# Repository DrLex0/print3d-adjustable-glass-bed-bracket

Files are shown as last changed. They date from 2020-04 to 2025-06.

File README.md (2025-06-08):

# Customizable Adjustable Glass Bed Bracket
*Customizable adjustable bracket for mounting glass plates on the print bed of 3D printers like the FlashForge Creator Pro (formerly thing:1949142)*

### License
[Creative Commons - Attribution - Share Alike](https://creativecommons.org/licenses/by-sa/4.0/)

### Attribution
This is a remix of multiple source models: the original ‘Flashforge Creator Pro Adjustable Glass Bed Bracket’ by chewbone ([Thingiverse thing:1291106](https://www.thingiverse.com/thing:1291106)), which was modified by omegatron ([Thingiverse thing:1296854](https://www.thingiverse.com/thing:1296854)), then by Lochemage ([Thingiverse thing:1940192](https://www.thingiverse.com/thing:1940192)), and then by me.

### Gallery

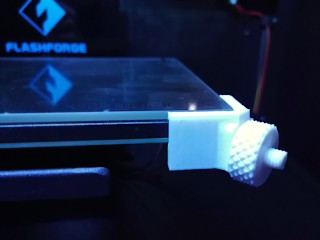
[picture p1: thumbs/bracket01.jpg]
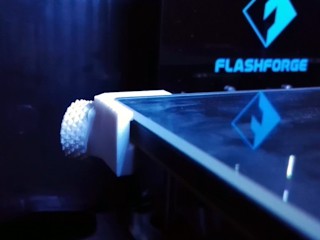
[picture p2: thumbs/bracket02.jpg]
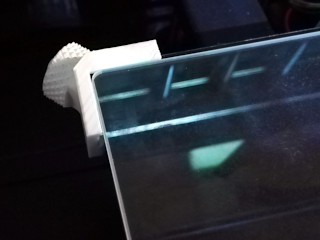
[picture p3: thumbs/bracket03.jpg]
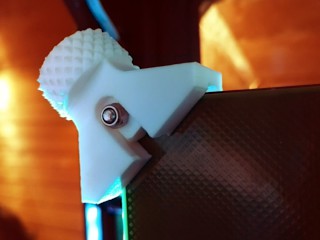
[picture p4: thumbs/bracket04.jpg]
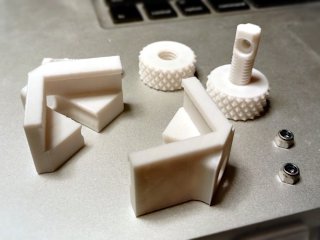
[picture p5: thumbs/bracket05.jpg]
Parts
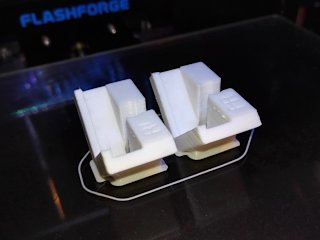
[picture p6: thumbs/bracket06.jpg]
Printing
[🔎](images/bracket01.jpg) [🔎](images/bracket02.jpg) [🔎](images/bracket03.jpg) [🔎](images/bracket04.jpg) [🔎](images/bracket05.jpg) [🔎](images/bracket06.jpg)

*Yes, there's quite a bit of text here, but it's worth it to read all of it. Even if you're familiar with Customizer and printing strong heat-resistant parts, you should still read the ‘Mounting’ and ‘Using’ sections for some important hints.*

## Intro

This is yet another iteration of the adjustable glass bed bracket. This time, not only the bracket itself is adjustable, so is the model! This customizable bracket fits the FlashForge Creator Pro and printers with similar build plates with M3 bolts at their corners. The adjustable knob makes it easy to swap out glass plates if you have more than one, so you can start printing on another plate while the first one is still cooling down.

The main advantage of this design is that it allows to mount the glass plate without anything sticking out above it. This means you never need to worry about the risk of your nozzles crashing into the brackets. This particular remix improves upon the originals by not sandwiching the bracket between the bed and the pin. This makes it much easier to adjust the bracket, and it also offers a more balanced mount.

If you have yet to buy a glass plate, try to find one that is just a few millimeters smaller than the bed in both the X and Y directions, and has rounded or beveled edges. Such plates work best with these brackets. **Borosilicate glass** is highly preferred over regular glass. Avoid plates thicker than 4 mm: they will take long to heat, and because glass is a rather good thermal insulator, their surface temperature will be a lot lower than expected.

*Obvious disclaimer:* I am not responsible for any possible damage caused by the use of these brackets, not if you follow my advice, and certainly not if you ignore it.
 

## Creating a customized bracket

Do not just print the example STL file, it is unlikely to fit your setup. Instead, open the `.scad` file in [OpenSCAD](https://www.openscad.org/) and **[use the OpenSCAD Customizer](https://www.dr-lex.be/3d-printing/customizer.html)** to generate brackets that match your particular bed and glass dimensions. The Customizer is limited to plates roughly the same width and depth as the heated bed itself.

If you are making brackets for a popular combination of printer model and glass bed, consider saving your parameters as a new customizer preset. The preset will be saved in the `.json` file and it would be nice if this would then be included in this repository, such that other users having the same printer and bed could simply load that preset from the customizer UI. To allow this, send me your updated `.json` file (for instance through a pull request).

Measure the *width, depth and height* (in other words *X, Y* and *Z* dimensions) of both the glass plate(s) and the bed (without glass). Next, enter those values in the corresponding fields in Customizer. Be as accurate as possible! Aim for at least 0.5 mm accuracy, this is possible with a simple ruler and a keen eye.
If you have multiple supposedly “identical” plates, there will often be small differences between them: take the *minimum* width and depth across all plates.

You can opt to mount the brackets on the front right and rear left corners, or front left and rear right. One pair of brackets is sufficient, but should you want to clamp all corners anyway, just run Customizer twice for both configurations. The models are marked so you know where to mount them: *FR = front right, FL = front left, RL = rear left, RR = rear right.*

The default is to center the glass on the print bed, but if you want to align one of its edges to an edge of the bed, you can select that in the options. For instance, I have aligned mine to the front edge because my start G-code chops off oozed filament on that edge.

You can choose to add an extra pair of tiny *ridges* that may help to keep the plate clamped down, an explanation can be found below.

The option *‘Rear Corner Fix’* in the advanced settings compensates for an oddness of the FFCP (at least mine). This is also explained below. Don't forget to disable this if you are generating brackets for printers with a different bed design.

If your glass plate is larger than the bed, you may want to enable *‘allowTabInset’* in the advanced settings to allow the glass to extend somewhat into the edges of the bracket. This option is disabled by default because it could make the bracket weaker. If the glass extends much more in one direction than the other, the inset will only occur for one edge to ensure alignment. Avoid that situation, and again: avoid plates larger than the bed altogether.

If the generated 3D model shows **“FAIL,”** then either you've entered non-numerical dimensions, or your glass plate is unfortunately too large or small to be compatible with the brackets. You can try to fiddle with the advanced settings if the dimensions are borderline, but it is advisable to find some other glass instead, that has nearly the same size as the bed.

### When to use the ‘Extra ridges’ option

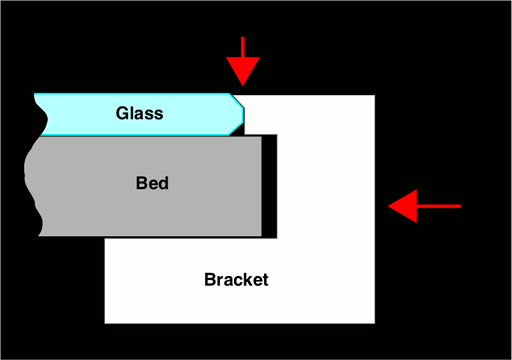
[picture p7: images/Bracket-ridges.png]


If your glass has beveled or rounded edges, it is worth it to enable the *‘Extra ridges’* option in Customizer. As the figure shows, the ridges can clamp down the glass by grabbing it on the bevel. This is not strictly necessary when using borosilicate glass, but regular glass or other materials that have a significant coefficient of expansion, are more likely to warp and lift at the edges when the bed is heated.

If you want to have the same clamp-from-above effect with glass that has straight edges, you can only do so by ignoring my advice of never letting anything stick out above the glass. If you make the brackets about 0.2 mm taller than the glass and enable the ridges, they will also clamp the glass from above. This is not worth the risk however: trying to clamp down the glass is *pointless* if you follow my usage instructions.

### When to enable/disable the ‘Rear Corner Fix’ option

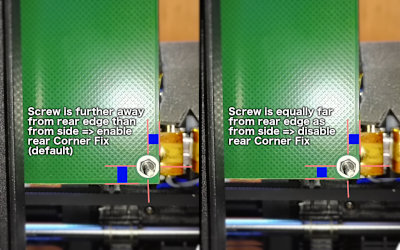
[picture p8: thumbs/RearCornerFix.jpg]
[🔎](images/RearCornerFix.jpg)

The bed on my FFCP isn't perfectly symmetrical and by default, the models will be generated to compensate for this. Check the bottom side of your heated bed at the rear (hint: use a mirror or take a snapshot with your smartphone) and compare it to the photo. If it looks like in the left photo, you don't need to change anything to the defaults. If it looks like in the right photo, disable the ‘Rear Corner Fix’ in the advanced settings.
 

## Choosing What Parts to Print

Next to the customized bracket model you created above, you will also need to print one pin and one nut (knob) per bracket. These are the choices you need to make:

* **Print spring-loaded knobs or not?** If you're willing to spend a little extra time molding silicone gaskets or printing them with a flexible filament, it is well worth it to print the spring-loaded knobs from the *SpringLoadedKnobs* folder instead of the plain ones. The springs ensure that the glass remains clamped regardless of differing thermal expansion of the heated bed versus the glass plate.
* **Print pins and nuts with fine or coarse thread?** The coarse thread is easier to print but offers rougher adjustment. I recommend to try the fine thread first.
* **Print regular or small knobs?** You only need the smaller ones if you have a thin bed and the regular size knob would stick out above the glass. Otherwise the regular ones are easier to adjust.
* **Print regular or extra long pins?** The *XL* versions of the pins are slightly longer than the normal ones. Only print the longer ones if necessary, because printing them in ABS or PC will be even more difficult than the shorter ones. If these still are too short, you definitely need to find a glass plate that more closely matches the size of the heated bed.
* **Print hollow or solid pins?** In most cases you should print the hollow one, it is less likely to warp during printing. Only use the solid one if you have a good reason. (There is no hollow version of the coarseThread because its shape leaves no room for a hollow space.)
 

## Printing

*This must be printed in a material that can withstand the heat of the heated bed!*

The model that comes out of Customizer is ready to print _without supports_. The worst overhangs are 45°, which should be easy to print if you have tuned your printer well. A fan can help with the overhangs but if you print ABS, either reduce fan speed if you can, or print hot and slowly.

If the pins seem too thick to fit inside the knobs, you can try re-printing the knobs scaled to 102% or more in the XY plane. (Mind that this is a sign that your printer is not printing accurately and you would be better off fixing the root cause of that problem than doing workarounds like this.)

I printed the nuts and pins at 0.1 mm, the bracket at 0.2 mm. I printed extra slowly for additional strength. I used a brim on the corner pieces, but this was probably unnecessary. Print the pins at 100% infill. Infill for the other parts doesn't really matter, but I do recommend to print them with 3 perimeters for strength. To get the best detail on the threads of the pin, print slowly with the fan enabled if necessary. If you really have trouble printing the pins, you might try printing them upright, or use the ‘coarseThread’ versions instead.

The **material** choice is important. Most crucial are the pins, because they are pushed against the heated bed, hence must be the most heat-resistant. What material you need, depends on the maximum temperature to which you will heat the bed during everyday use.
From best to worst, here are some choices for the most common filaments:
* **Polycarbonate (PC):** this is an excellent material because it can withstand all reasonable heated bed temperatures, therefore if you print the brackets with it, you will never have to worry about the bed temperature. I would recommend it if you will often print ABS at bed temperatures near 110°C. Unfortunately PC is difficult to print with. The absolute minimum extruder temperature is [260°C](http://reprap.org/wiki/Polycarbonate#Heater_Settings). You need an all-metal hot-end to print at that temperature, because the teflon liners in standard hot-ends will quickly degrade at that temperature, releasing toxic fumes. You can of course order a PC print through a service like 3DHubs. If price is an issue, it is OK to have only the pins printed in PC, and print the brackets and knobs yourself in ABS.
* **ABS:** this is a good material because it will not easily deform below 110°C. If you will mostly print PLA and PETG, and only occasionally ABS, then ABS brackets are perfectly OK. You might need to print new pins from time to time because they may bend after a while. To minimize deformation, always follow the instructions from the *Mounting* and *Using* sections!
* **PETG:** this is good if you will never heat the bed above 75°C, e.g. if you'll only print PLA and occasionally PETG. Don't use it if you will ever have to do an ABS print though.
* **PLA:** I would not recommend this, unless you'll never heat the bed above 55°C. If you would ever need to heat the bed above 60°C, your PLA pins and brackets will deform or melt.

I have used ABS printed pins for about half a year, after this they were somewhat bent but still usable. I printed new pins in polycarbonate, and I expect those to last forever.

If you're the [AvE](https://www.youtube.com/user/arduinoversusevil) kind of guy and have the tools and skills for metalworking, an alternative to obtain perfectly heat-resistant pins, is to buy stainless steel M8 × 1.25 bolts and transform them into the shape of the pins, or create the shape from scratch. Stainless steel is ideal due to its low thermal conductivity, which reduces the need for heat-resistance of the other parts of the bracket.
 

## Mounting

This design differs from the originals it was remixed from, in that you do not need to unscrew any of the existing nuts or bolts (except possibly on newer printers, see below). Instead, you need an additional M3 nut per pin. I recommend to use *nyloc* nuts. Mount the pin with the recess upwards, covering the existing M3 nut, and tighten the pin with the extra M3 nut ([this tool](https://www.thingiverse.com/thing:1959962) may come in handy).

See the following rendered 3D image for an illustration of how the complete assembly fits together. Again, even though this image shows the screws separately, you do not need to remove them. This was only rendered as such to help people who are building their printer from scratch.

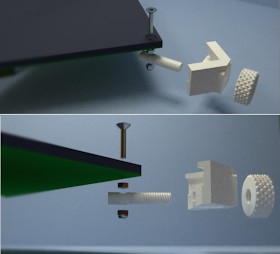
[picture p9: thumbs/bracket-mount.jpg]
[🔎](images/bracket-mount.jpg)

*Important:* only tighten the M3 nut just to the point where the pin can no longer move vertically. Do not tighten it further, unless you printed the pin in polycarbonate or will never heat the bed anywhere near 110°C.

If you don't have any M3 nuts to spare, you can also print the pin from [omegatron's original model](http://www.thingiverse.com/thing:1296854) and mount it using the existing nut, with the recess downwards. I do recommend using my version of the pin if possible.

*Note:* the Creator Pro used to ship with bolts on the corners of the print bed that were about 20 mm long in total, making them stick out about 11 mm below the bed. It seems that recently FlashForge switched to shorter bolts, which makes it impossible to mount the pins as-is. If this is the case for your printer, you will need to replace the bolts with longer ones. Look for 20 mm M3 bolts with a flat head, preferably also with a hex socket.
 

## Using

If you use the *spring-loaded knobs,* read the instructions from their README, and skip the following paragraph because those knobs make it redundant.

Otherwise, the correct workflow is to first **preheat** your bed with the glass plate on top, and only tighten the knobs when the temperature is stable. The reason is that borosilicate glass has a much lower thermal expansion coefficient than the bed, therefore if you would tighten it cold and then heat, the bed will become larger w.r.t. the plate, and it may be loose enough to wiggle around. The whole point of these brackets is that it is very easy to adjust them, so it is better to adjust them when not really necessary, than *not* to adjust them when needed.

Do not tighten the knobs like crazy. Just tighten them up to the point where the glass cannot move. Over-tightening may cause the plastic to deform, or the plate to lift if you did not print the brackets with accurate dimensions.
 

### Should you remove the blue sheet or BuildTak when using a glass plate?

If you don't foresee that you will ever print on the sheet again, you should remove it. The sheet acts as an insulator and will cause a drop in temperature between the bed and glass, as much as 10°C depending on the temperature and thickness of the sheet. One small advantage of leaving the sheet installed, is that it provides some friction, making it less easy for the glass to slide around than on the bare metal surface. However, it should be the brackets that keep your glass in place, not the surface.

## How I Designed This

I took omegatron's model, cleaned it up in Blender, and chopped off all the parts that would vary when making it customizable. I exported it to STL, and converted this to an OpenSCAD polyhedron using stl2scad, because Customizer does not allow importing STL files. Then I added the necessary customizable shapes using the usual SCAD magic.

After 8 years, someone notified me that the fine screw threads of the pin and nuts didn't match… yeah. This flaw has been in the models since chewbone's original. It somehow still worked in most cases, but I finally corrected the threads in the v4 nut STL files for optimum performance.

## Updates

### 2016/12/11
I updated the pin model to be longer at the side of the bed. This should make it more resistant against deformation. If you print new pins, be sure to use this new model. Remember: do not tighten the pins any harder against the bed than necessary. Otherwise you'll end up with the counter-intuitive situation where the pin becomes the more loose, the more you tighten it.
Included *‘divided’* variation of the pin model (this had a cavity that might allow to print the threaded part with less infill, however this was unpractical so I removed it again).

### 2016/12/12
Allowed larger range of values in customizer: bed thickness can now go down to 5 mm and tabs can go up to 7 mm.

### 2016/12/27
Added smaller nuts and coarse-threaded variants (using the same threads as Lochemage's remix of the original brackets).

### 2017/05/09
Completely overhauled Customizer so it is much easier to use, and offers a wider range of parameters.
Created [Spring-loaded Knobs remix](http://www.thingiverse.com/thing:2313598), which I highly recommend over the plain knobs.

### 2017/05/14
Added ‘Rear Corner Fix’.
2017/06/04: Bumped default tabWidthOffset from 1.2 mm to 1.5 mm.

### 2017/06/18
Added a version of the regular pin with the threaded section hollowed-out. This makes it less likely to warp when printed in ABS or polycarbonate.
Fixed the broken preview in Customizer/OpenSCAD.
Minor update 2017/07/25: made error messages in customizer preview more readable.

### 2017/08/19
Added XL versions of the pins, these are about 6mm longer.
Wasted some of my precious time due to the stupid “Token Expired” bug in the Thingiverse site. If this kind of crap keeps happening, I'll just stop uploading models altogether.

### 2019/04/07
Added (advanced) option to change the length of the sides of the bracket.

### 2025/06/08
Fixed the incorrect fine screw thread pitch of the nut models, the new ones are now called ‘v4’.

## TAGS:
`Adjustable`, `customizable`, `customizer`, `FFCP`, `FFCPRo`, `glass`, `Glass_bed`, `Glass_bed_holder`, `openscad`, `supportless`

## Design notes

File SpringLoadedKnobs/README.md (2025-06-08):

# Spring-loaded Knobs for Adjustable Glass Bed Bracket
*Knobs with built-in spring action for adjustable glass bed brackets (formerly thing:2313598)*

### License
[Creative Commons - Attribution - Share Alike](https://creativecommons.org/licenses/by-sa/4.0/)

### Attribution
See attribution info in the top-level README.

### Gallery
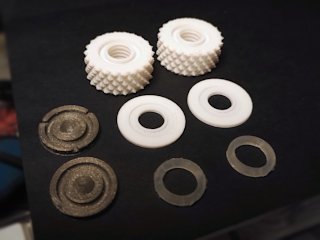
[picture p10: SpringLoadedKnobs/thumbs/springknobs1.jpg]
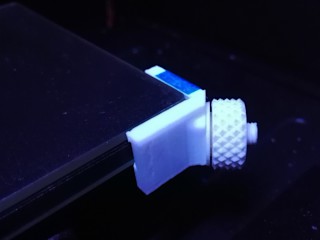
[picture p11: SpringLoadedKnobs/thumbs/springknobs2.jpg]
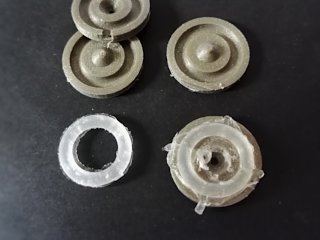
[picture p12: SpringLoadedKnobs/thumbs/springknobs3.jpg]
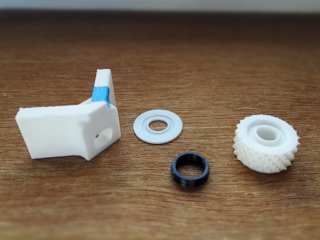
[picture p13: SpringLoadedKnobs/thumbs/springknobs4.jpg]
Photo 4 - TPU spring
[🔎](images/springknobs1.jpg) [🔎](images/springknobs2.jpg) [🔎](images/springknobs3.jpg) [🔎](images/springknobs4.jpg)

## Description and Instructions

These are improved knobs for the Customizable Adjustable Glass Bed Bracket for the FlashForge Creator Pro and similar printers. These knobs have a **silicone gasket** incorporated in them, which acts as a spring. As an alternative, you can print the springs using a **flexible filament.**

The problem with the original knobs and many other bracket designs, is that the thermal expansion of the aluminium bed is much larger than that of the glass (especially borosilicate glass). This means if you tighten the knobs while the bed is cold and then heat it, it becomes larger than the glass. This causes the brackets to lose their grip, allowing the glass to shift around.

These spring-loaded knobs solve that problem by keeping on pushing against the brackets even if they move inwards a little due to the bed expanding. The gaskets are just thick enough to offer the required spring travel, without being too thick to make the brackets wobbly.

Some assembly and patience is required: you need to create your own silicone gaskets with a printable mold, or you can print them with a flexible filament. I provide molds for 3.5 mm and 4 mm tall gaskets. Which one is most suitable, will depend on how flexible the silicone compound is that you will be using. I suggest to simply print both molds, make two pairs of gaskets, and see which ones work best.
 

## Method 1: make gaskets using silicone compound

Carefully read the instructions on the [Customizable Gasket Mold Maker page](https://www.thingiverse.com/thing:2287689). In a very short nutshell: print the molds in **ABS,** as it seems to adhere the least to silicone compound. Use **RTV silicone** if you can.
If you want even thicker gaskets, you can make your own with Customizer on that page. The inner diameter must be *10 mm* and the outer diameter *14.1 mm.* You could also try a gasket with a square profile to increase stiffness.

The nice thing is that you can already use the knobs without the gaskets while you're waiting for them to cure. You only need to remember to manually re-tighten the knobs after preheating the bed. Once you have the gaskets, unscrew the knobs, drop in the gaskets, and you're good to go.

### Preparing the gaskets for use

Cut or pry off any excess silicone from the gaskets to make them nice and round. Make sure the gaskets are fully cured before assembling the knobs. RTV silicone gaskets should be ready to use, but for regular silicone, you should leave the gaskets in the open air for at least 24 more hours, probably longer for neutral cure compound. This allows them to cure further and release solvents still contained inside. Again, exposing them to humidity may speed up this process.
 

## Method 2: print gaskets/springs with flexible filament

If you have a sufficiently flexible filament, you can print an effective spring instead. The `Gasket-TPU-printable` STL file can be printed as-is in TPU. Infill doesn't matter because the model is a hollow shape. The filament must be elastic and reasonably heat-resistant. I have tried this in NinjaFlex which seems to work well. Anything much harder than Shore 85A is likely to be too stiff to act as a spring.
 

## How to use the knobs

Remove any remains of hairspray or glue stick from the bottom of the disks and brackets, to ensure these parts can easily slide against each other, otherwise tightening the knobs could be difficult. A wee bit of silicone grease/oil can help as well, you may need to re-apply this occasionally. Assemble and mount the knobs as shown in the photos.

You can adjust the knobs in two ways:
1. Preheat the bed to the highest temperature you'll use, and then tighten the knobs just beyond the point where the glass can no longer move.
2. Just tighten the knobs with the bed cold, to the point where there is only a tiny gap left between the disk and the knob.

Either method is OK, but the first one is preferred because it minimizes the amount of stress on the brackets and could prolong their lifespan. If you're not going to print for a while, it is advisable to loosen one of the knobs.

If you made the gaskets with regular silicone compound, they will be quite soft when freshly made, and become harder over the course of the next weeks. This means you may need to tighten the knobs more with freshly made gaskets.
 

## Printing

For the **knobs/nuts:** as with the originals, **ABS** is recommended for heat resistance. Print slowly and if possible, provide moderate cooling to get an accurate result. See the main README in the top level of this repository for more details.

All these parts should be printed at 0.1 mm layers. Infill doesn't really matter.

The knobs are available in both fine and coarse threads, and normal and small sizes, like the originals. Print the knob that matches the pin thread and bracket height you're using. You should print the normal size knobs unless you have a very thin bed that would cause the knobs to stick out above the glass.

For the **gasket mold:** again see the [Customizable Gasket Mold Maker page](https://www.thingiverse.com/thing:2287689) for instructions. In a very short nutshell: use **ABS** because it seems the least sticky to the silicone.
To avoid that the tip of the alignment cone becomes a molten blob due to short layer print times, you can try to:
* print two molds at once. You'll need two gaskets anyway, and making them at once will save you a lot of waiting time. It isn't worth it to try saving a few grams of filament by only printing one mold!
* print the molds together with something else to increase the time between layers.
* provide all the cooling you can muster while the cone is being printed.

For the **printable gasket/spring:** just print it in a sufficiently flexible/elastic filament, like NinjaFlex or similar. When in doubt, set infill to 100% although this shouldn't matter because the model is hollow.
 

## Background Information

The reason why I chose silicone gaskets as springs, is that silicone does not easily lose its shape over time, it is quite heat-resistant, and most importantly, everyone can easily make their own gaskets with a 3D printed mold! Any other 3D printed glass bed bracket that relies on springiness of the shape itself, is pretty much doomed to deform over time, especially when heated near 110°C. These knobs on the other hand should last a long time.

## Updates

### 2020/03/07
Added printable spring/gasket that should work well in a soft TPU like NinjaFlex.

### 2025/06/08
Fixed the incorrect fine screw thread pitch of the nut models, the new ones are now called ‘v4’.

## TAGS

`Adjustable`, `FFCP`, `FFCPRo`, `glass`, `Glass_bed`, `Glass_bed_holder`, `knob`, `nut`, `silicone_mold`, `spring_loaded`

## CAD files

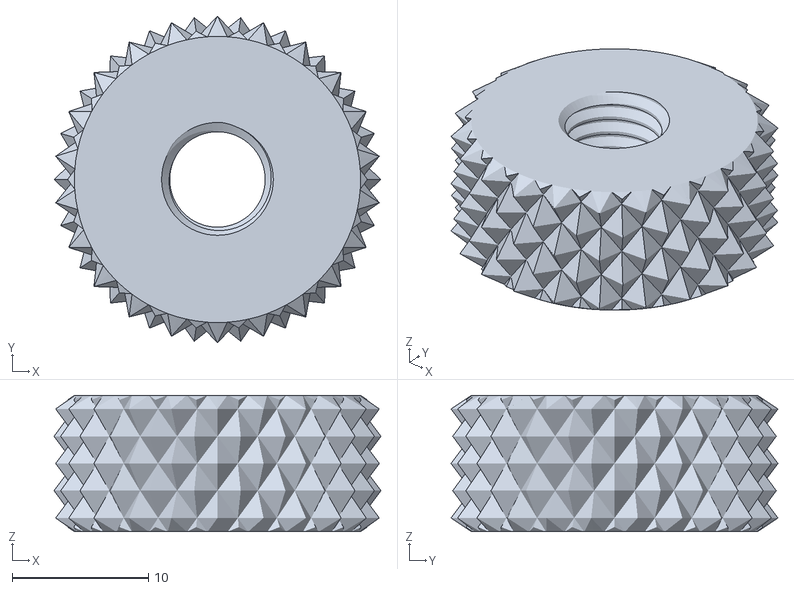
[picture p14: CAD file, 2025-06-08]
GlassBedNut-v4.stl
24.0 x 24.0 x 10.0

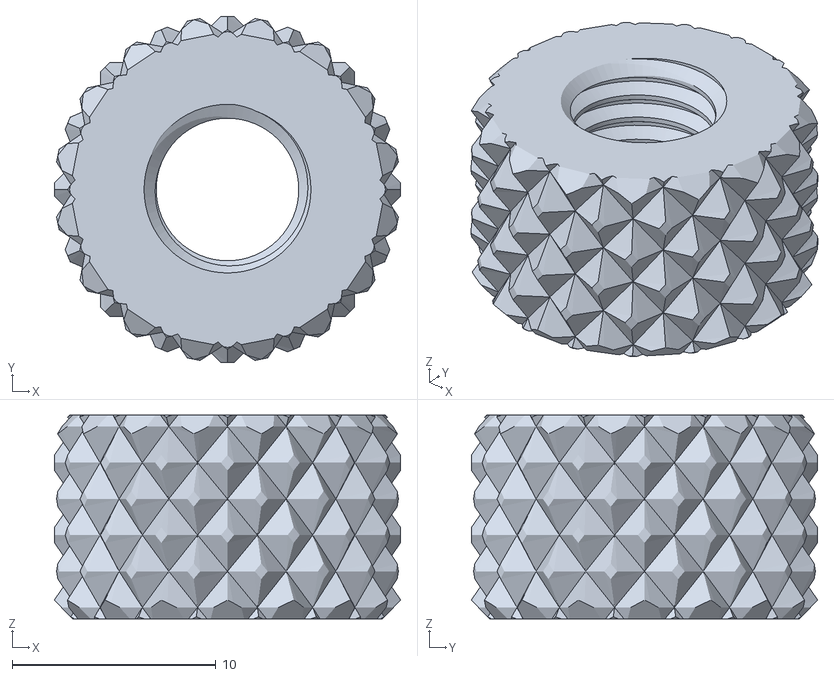
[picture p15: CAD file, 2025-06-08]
GlassBedNut-v4-small.stl
17.0 x 17.0 x 10.0

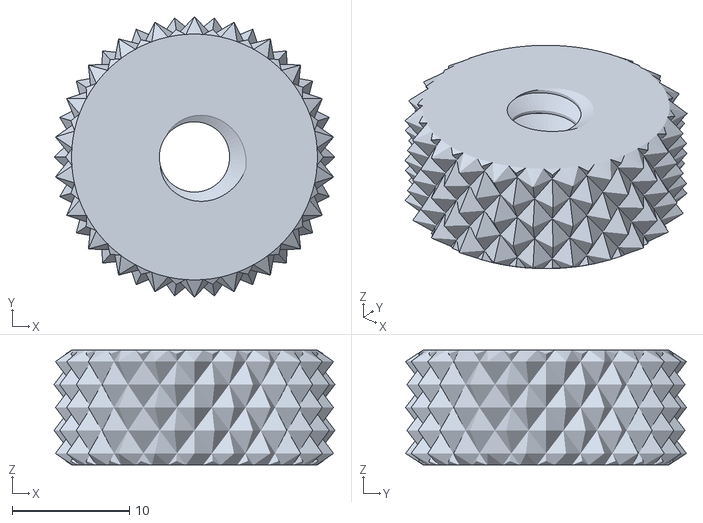
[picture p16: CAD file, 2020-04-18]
GlassBedNut-coarseThread.stl
24.0 x 24.0 x 9.80

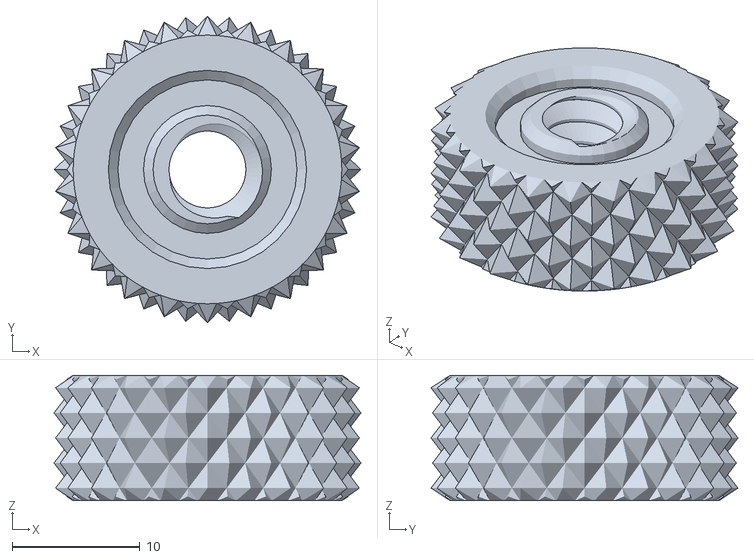
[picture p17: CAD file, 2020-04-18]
SpringLoadedKnobs/GlassBedNut-coarseThread-Spring.stl
24.0 x 24.0 x 9.80

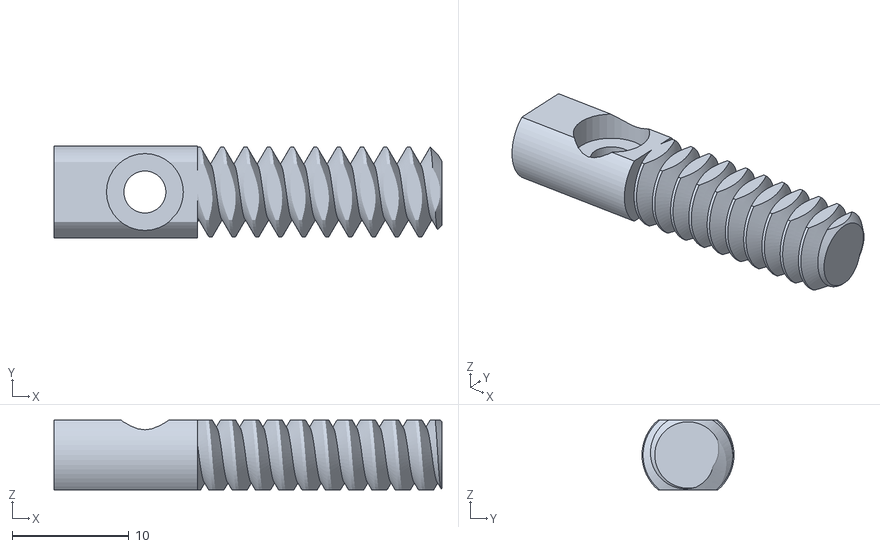
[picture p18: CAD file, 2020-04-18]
GlassBedPin-coarseThread.stl
33.3 x 7.90 x 6.00

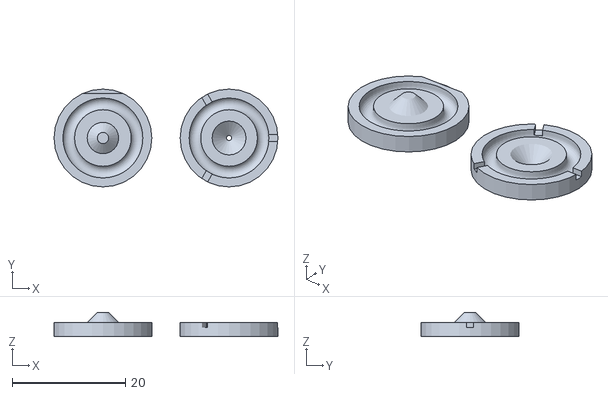
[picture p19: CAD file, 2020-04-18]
SpringLoadedKnobs/GasketMold3_5mm.stl
39.6 x 17.3 x 4.33

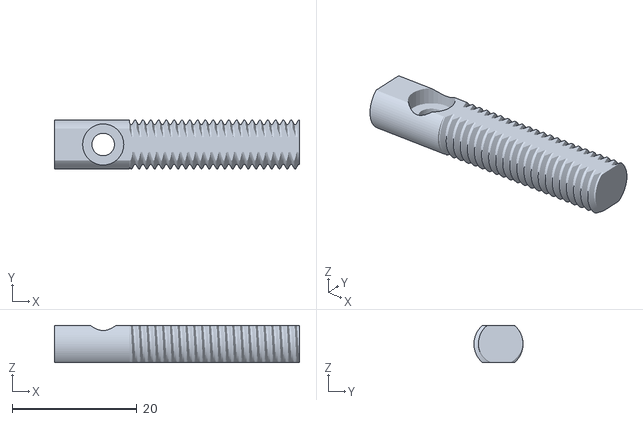
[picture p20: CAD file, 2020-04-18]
GlassBedPin-XL.stl
39.3 x 7.87 x 6.00

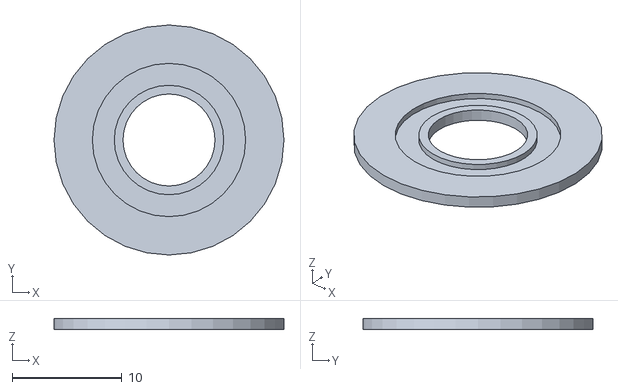
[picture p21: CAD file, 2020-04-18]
SpringLoadedKnobs/GlassBedNut-disk.stl
21.0 x 21.0 x 1.00

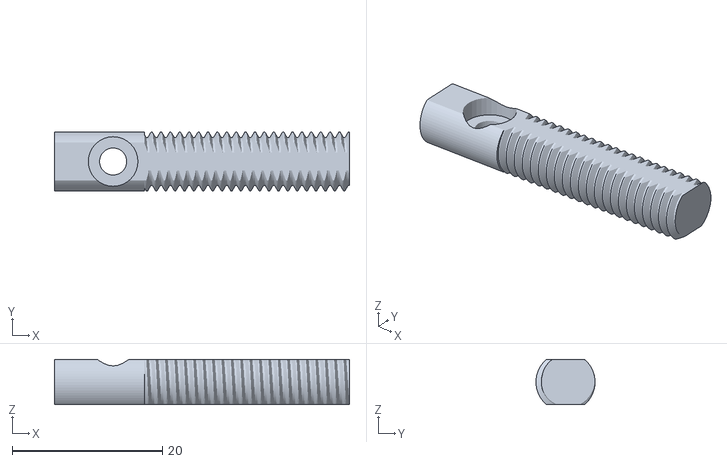
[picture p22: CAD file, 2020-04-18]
GlassBedPin-hollow-XL.stl
39.3 x 7.87 x 6.00

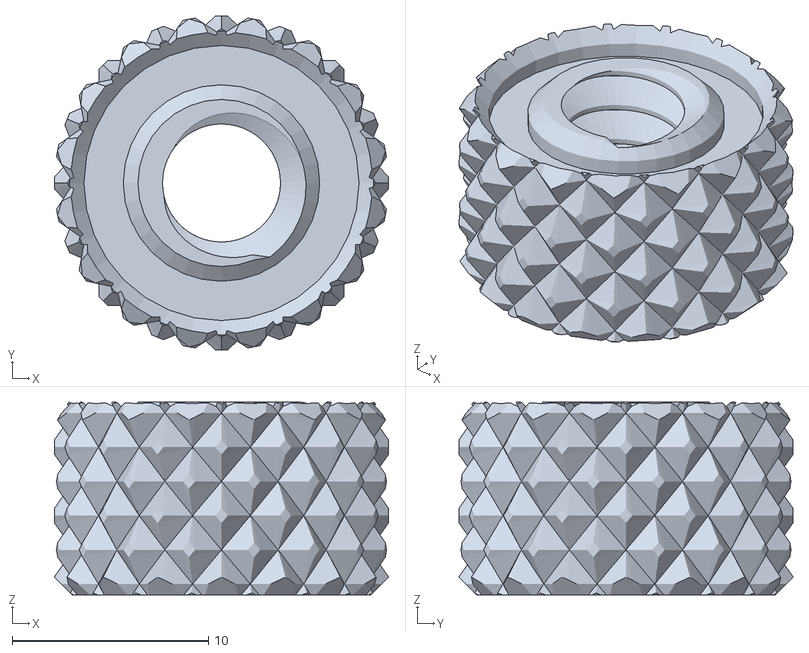
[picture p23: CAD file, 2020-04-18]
SpringLoadedKnobs/GlassBedNut-coarseThread-Spring-small.stl
17.0 x 17.0 x 9.80

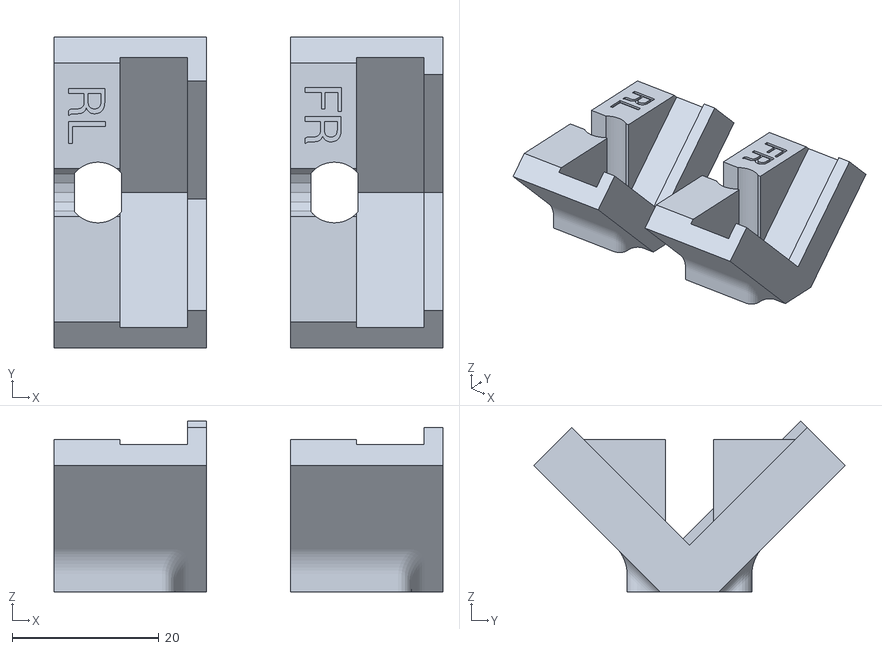
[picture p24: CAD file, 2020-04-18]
GlassBedCorner-example-doNotUse-useCustomizer.stl
53.0 x 42.4 x 23.3

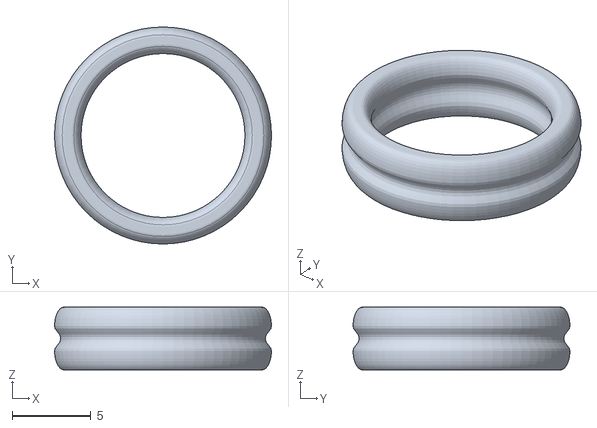
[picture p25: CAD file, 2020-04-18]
SpringLoadedKnobs/Gasket-TPU-printable.stl
13.8 x 13.8 x 4.00

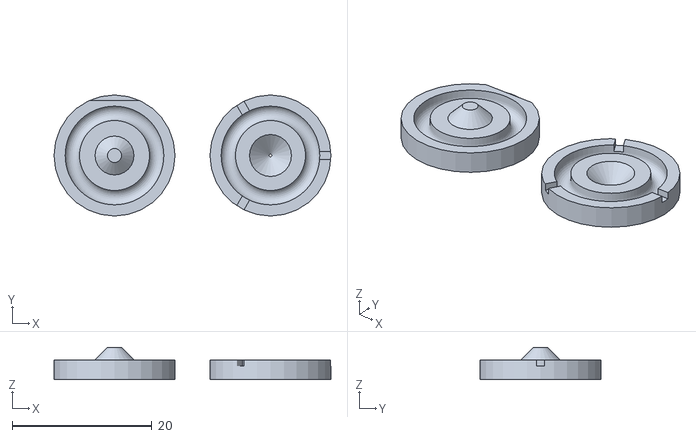
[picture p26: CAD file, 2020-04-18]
SpringLoadedKnobs/GasketMold4mm.stl
39.6 x 17.3 x 4.58

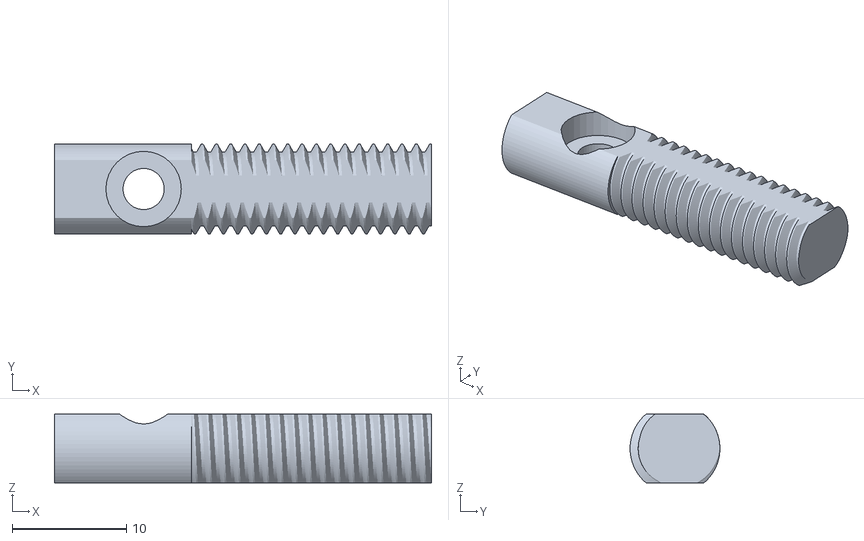
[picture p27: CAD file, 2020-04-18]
GlassBedPin-hollow.stl
33.0 x 7.87 x 6.00

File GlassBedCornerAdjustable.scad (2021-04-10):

/* Adjustable Glass Bed Corner for FlashForge Creator Pro
 * By DrLex, v2.4.1 2021/04
 * Released under Creative Commons - Attribution - Share Alike license */

/* [Dimensions] */
// The width of the aluminum plate of your heated bed (X axis). Enter all values in millimeters.
bedWidth = 231; //[50:.1:400]

// The depth of your heated bed (Y axis)
bedDepth = 153.5; //[50:.1:400]

// The total thickness of your heated bed (Z) except the glass. This includes the heater PCB at the bottom and anything stuck to the top. You should also add a margin to ensure the corners will easily fit, I recommend to add 0.25mm. The default (9.2) is for the bed that came with my FFCP, with the blue surface stuck to it. Without the surface, it is 8.6mm.
bedThickness = 9.2; //[3:0.05:12]

// The width of your glass plate (X). If you have multiple and they vary slightly, take the smallest value.
glassWidth = 226.8; //[50:.1:400]

// The depth of your glass plate (Y). Same remark as above.
glassDepth = 149.3; //[50:.1:400]

// The thickness of your glass plate (Z)
glassThickness = 3.0; //[2.0:0.05:10]

/* [Options] */
// Where you want to mount the brackets. If you want all 4 corners, run Customizer twice, once for each option.
bracketPositions = "FrontRight+RearLeft"; //[FrontRight+RearLeft, FrontLeft+RearRight]

// Add a small ridge at the top of the tabs, this may help to clamp down the plate especially if it has rounded edges.
extraRidges = "no"; //[yes, no]

// How to align the glass plate to the bed in the X direction. Center is probably preferable.
xAlign = "center"; //[center, left, right]

// How to align in the Y direction. Depending on your start G-code, 'front' may be a good choice.
yAlign = "center"; //[center, front, rear]

/* [Advanced] */
// This is the height of the holding tabs relative to your glass thickness. A small negative value (e.g. -0.4mm) is recommended to ensure the tabs will never stick out above the glass.
tabHeightOffset = -0.4; //[-2.0:0.1:3]

// This value is added to the exact tab width, at least 1mm is recommended to provide some margin and account for thermal expansion of the bed. At least 1.5mm is recommended to compensate for measuring inaccuracies.
tabWidthOffset = 1.5; //[0:0.1:3]

// Allow to use a negative tab width if the glass is much larger than the bed. This might allow to fit really large glass plates, although you should avoid doing that altogether.
allowTabInset = "no"; //[yes, no]

// Compensate for the fact that the rear screws on the FFCP are a bit further away from the rear edge than expected. Disable if this is not the case on your heated bed.
rearCornerFix = "yes"; //[yes, no]

// Length of the sides. Mind that you won't gain much extra stability by making the bracket larger, this may even increase the risk of it deforming. Only change this if you know what you're doing.
edgeLength = 26.0; //[22.0:0.1:50.0]

/* [Hidden] */
// Fixed and derived dimensions
edgeLengthTop = 51.3;
edgeOffset = 2.815;
minInset = allowTabInset == "no" ? 0 : -2.5;
edgeHeight = glassThickness + tabHeightOffset;
topChop = 2.3829 + edgeLength * 0.707107;
labelZ = topChop - 0.408;
sideChop = 1.185 + edgeLength;

module renderBracket(extendL, extendR, label1, label2) {
    // Extra widths must be added to both tabs to maintain the 45deg angle
    extraL = extendL < minInset ? minInset - extendL : 0;
    extraR = extendR + extraL < minInset ? minInset - (extendR + extraL) : 0;
    tabWidthLeft = extendL + extraL + extraR;
    tabWidthRight = extendR + extraL + extraR;
    edgeWidthLeft = 4 + tabWidthLeft;
    edgeWidthRight = 4 + tabWidthRight;
    
    if(tabWidthLeft > 8 || tabWidthRight > 8) {
        linear_extrude(1) {
            translate([0, 9]) text("FAIL!", 12, font="Roboto", halign="center");
            text("Incompatible", 7, font="Roboto", halign="center");
            translate([0, -9]) text("dimensions", 7, font="Roboto", halign="center");
        }
    }
    else {
        difference() {
            union() {
                difference() {
                    baseShape();
                    
                #   rotate([45,0,0]) translate([bedThickness,1.185+tabWidthRight,1.185+tabWidthLeft]) cube(size=[edgeHeight+0.5,edgeLength-2,edgeLength-2]);
                    translate([bedThickness+edgeHeight,-25,-1]) cube(size=[10,50,30]);
                    translate([-7, 10.7, labelZ]) rotate([0, 0, -90]) linear_extrude(1, convexity=2) text(label1, 5, font="Roboto", halign="center");
                    translate([-20, -50, topChop]) cube(size=100);
                    if(label2 != undef) {
                        translate([-7, -10.7, labelZ]) rotate([0, 0, -90]) linear_extrude(1, convexity=2) text(label2, 5, font="Roboto", halign="center");
                    }
                }


                difference() {
                    union() {
                        // 'Left' edge
                        rotate([45, 0, 0]) translate([bedThickness, -2, -edgeOffset]) cube(size=[edgeHeight,edgeLengthTop+2,edgeWidthLeft]);
                        // 'Right' edge
                        rotate([-45, 0, 0]) translate([bedThickness, -edgeLengthTop, -edgeOffset]) cube(size=[edgeHeight,edgeLengthTop+2,edgeWidthRight]);
                        
                        if(bedThickness > 10) {
                            // The model doesn't extend that high, so fill in the gap.
                            rotate([45, 0, 0]) translate([10, -2, -edgeOffset]) cube(size=[bedThickness-10,edgeLengthTop+2,4]);
                            // 'Right' edge
                            rotate([-45, 0, 0]) translate([10, -edgeLengthTop, -edgeOffset]) cube(size=[bedThickness-10,edgeLengthTop+2,4]);
                        }
                        
                        if(extraRidges == "yes") {
                            ridgeHeight = edgeHeight/3;
                            ridgeStart = bedThickness + 2*ridgeHeight;
                            rotate([-45, 0, 0]) translate([ridgeStart, -tabWidthLeft-1.185, -2]) linear_extrude(height=edgeLengthTop+2) polygon(points=[[0,0], [ridgeHeight,0], [ridgeHeight,-0.6]]);
                            rotate([45, 0, 0]) translate([ridgeStart, tabWidthRight+1.185, -2]) linear_extrude(height=edgeLengthTop+2) polygon(points=[[0,0], [ridgeHeight,0], [ridgeHeight,0.6]]);
                        }
                    }
                    
                    // Chop off the bottom
                    translate([0,-10,-20]) cube(20);
                }
            }
            
            // Chop off slanted sides
            rotate([45, 0, 0]) translate([-20,-15,sideChop]) cube(size=50);
            rotate([-45, 0, 0]) translate([-20,-15,sideChop]) cube(size=50);
        }
    }
}

extendWL = tabWidthOffset + (xAlign == "center" ? (bedWidth - glassWidth) / 2 :
                            (xAlign == "left" ? 0 : bedWidth - glassWidth));
extendWR = tabWidthOffset + (xAlign == "center" ? (bedWidth - glassWidth) / 2 :
                            (xAlign == "right" ? 0 : bedWidth - glassWidth));
extendDF = tabWidthOffset + (yAlign == "center" ? (bedDepth - glassDepth) / 2 :
                            (yAlign == "front" ? 0 : bedDepth - glassDepth));
extendDR = tabWidthOffset + (yAlign == "center" ? (bedDepth - glassDepth) / 2 :
                            (yAlign == "rear" ? 0 : bedDepth - glassDepth));

if(extendWL == undef || extendWR == undef || extendDF == undef || extendDR == undef) {
    linear_extrude(1) {
        translate([0, 9]) text("FAIL!", 12, font="Roboto", halign="center");
        text("Please enter dimensions in", 7, font="Roboto", halign="center");
        translate([0, -9]) text("millimeters only, e.g. '123.4'.", 7, font="Roboto", halign="center");

    }
}
else {
    // To compensate for the asymmetric placement of the screw, pretend the bed is 2.5mm wider at the rear
    extendWExtra = rearCornerFix == "yes" ? 1.25 : 0;
    shift = 10 + (bedThickness + glassThickness) / 2;

    if(bracketPositions == "FrontRight+RearLeft") {
        translate([shift, 0, 0]) renderBracket(extendWR, extendDF, "FR");
        translate([-shift, 0, 0]) renderBracket(extendWL + extendWExtra, extendDR, "RL");
    }
    else {
        translate([shift, 0, 0]) renderBracket(extendDF, extendWL, "FL");
        translate([-shift, 0, 0]) renderBracket(extendDR, extendWR + extendWExtra, "RR");
    }
}
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

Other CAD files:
SpringLoadedKnobs/GlassBedNut-v4-Spring.stl
SpringLoadedKnobs/GlassBedNut-v4-Spring-small.stl
GlassBedPin-coarseThread-XL.stl
SpringLoadedKnobs/GlassBedNut-disk-small.stl
GlassBedNut-coarseThread-small.stl
GlassBedPin-roundSlot.stl

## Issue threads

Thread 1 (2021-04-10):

Allow hundredths of millimeter in bedThickness value for GlassBedCornerAdjustable.scad

loshlee, 2021-04-10:
Suggest "bedThickness = 9.20; //[3:0.01:12]" rather than "bedThickness = 9.2; //[3:0.1:12]" because current doesn't allow setting hundredths of millimeter (you suggest adding .25mm in explanation).

DrLex0, 2021-04-10:
Hundredths of a millimeter would be pretty pointless considering the accuracy of most 3D printers. I changed it to .05 mm increments which is still realistic.

loshlee, 2021-04-10:
OK, thanks. I really love the brackets, BTW. Printed them in ABS. Thanks again.

Sincerely,

Laine Lee

On 4/10/21, 7:51 AM, "Alexander Thomas" ***@***.***> wrote:

Hundredths of a millimeter would be pretty pointless considering the accuracy of most 3D printers. I changed it to .05 mm increments which is still realistic.

—
You are receiving this because you authored the thread.
Reply to this email directly, view it on GitHub, or unsubscribe.

Closed 2021-04-10.

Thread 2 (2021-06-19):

Add pin length parameter for CR-10/Ender 3 beds

DJLuigi10, 2021-06-19:
I have an ender 3 and the hotbed screws are approximately 48mm diagonally from the bed corner. The XL pins are still way short of being useable, unless I opt to drill some holes in my hotbed, which I'm not too keen to do.

I would love to be able to adjust the length of the pins and/or depth of the underhanging portion of the bracket to accomodate as I really like this design, and would love to be able to make use of this exquisitely designed part.

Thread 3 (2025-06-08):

Threads of GlassBedNut-small and GlassBedNut-V3 don't match anything

Poikilos, 2025-06-08:
These don't match anything:
- GlassBedNut-small
- GlassBedNut-V3

They are finer than the course thread (GlassBedPin-coarseThread, GlassBedPin-coarseThread-XL) and courser than the fine thread (GlassBedPin-roundSlot, GlassBedPin-hollow, GlassBedPin-hollow-XL, GlassBedPin-XL).

I am using the ThingiVerse copy, but the repo says you are still using the ThingiVerse copy on here so the issue still needs to be fixed here.

I used them anyway on a FlashForge Creator Pro 2016, but they don't go on right. I thought maybe you made them intentional for a friction fit, but I fixed the threads and they work well (On my changed version which accepts a spare m3 screw to work with the MakerBot Replicator 2X--I'll provide that separately)...Also, there is pretty much no way they would back out, so matching threads is best.

DrLex0, 2025-06-08:
Sometimes it does seem like someone changed the Matrix. This model has existed since the end of 2016, and after thousands of downloads, you're the _first_ to report this blatant error which already existed in chewbone's original and got copied across each remix, including mine.
Well, it seems that despite the mismatched threads, it worked in most cases. I did always have the feeling that the threads acted weird, but I attributed it to printing inaccuracies. The models have now been updated with correct threads. Thanks for reporting this!

Closed 2025-06-08.

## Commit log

2020-04-18 Thingiverse exodus model 6: migrate to GitHub
    [Gasket-TPU-printable.stl, GasketMold3_5mm.stl, GasketMold4mm.stl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]
2020-04-18 Provide ranges for all values
    [GlassBedCornerAdjustable.scad]
2020-07-05 More consistent file names; tweak README
    [GlassBedNut-coarseThread-Spring-small.stl, GlassBedNut-coarseThread-Spring.stl, GlassBedNut-coarseThread-small.stl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]
2020-07-05 Fix typo
    [GlassBedCornerAdjustable.scad]
2021-04-10 Allow finer increments in bed and glass thickness
    [GlassBedCornerAdjustable.scad]
2025-06-08 Fix issue #3: correct fine screw thread pitch in nut models
    [GlassBedNut-Spring-small.stl, GlassBedNut-Spring.stl, GlassBedNut-small.stl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]
